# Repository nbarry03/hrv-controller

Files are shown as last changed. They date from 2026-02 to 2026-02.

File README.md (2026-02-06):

# HRV Controller
>**Warning: This is an overview and is not intended to be an exhaustive guide. Use your own judgement and don't burn your house down.**

This project was created to control an HRV system with a [4 wire remote](https://my.daikinnortheast.com/product/control-ventilation-advanced-wall/01tRn000006Wke3IAC). Many smart thermostats can integrate with and control an HRV, but my thermostat only works with 2 wire remote systems, and therefore could not directly be connected.

An ESP8266 with a DAC was used to spoof the remote signals described below, triggering the HRV to run based on the combination of voltages. Because the ESP8266 has wifi and can be integrated into ESPHome, this allows me to use ESPHome to write firmware and control the state of the remote through Home Assistant, or in my case, controlled by AppDaemon and interacting with HASS via the AppDaemon HASS integration.

# The remote
The remote has 4 modes; econo, vent, 20 min/hr, and off. Econo runs the system with a low fan speed, while 20 min/hr runs at max speed but intermittently. Vent runs the system with the fan max speed. The control voltages for each mode are summarized below, with the wire color and remote terminal label denoted as follows: `Wire color (remote label)`.

| Mode | Red (R) | Blue (Bl) | Green (G) | Black (W) |
| --- | --- | --- | --- | --- |
| **Econo** | 5V | - | 3.4V | 3.1V |
| **Vent** | 5V | - | 3.4V | 3.1V |
| **20 min/hr** | 5 | - | 4.4V | 2.0V |
| **Off** | 5V | - | 1.4V | 2.0V |

> ***Note:** The black wire connected to the W terminal.

Based on the measured voltages there are 2 signal wires, green (G) and black (W), with voltage from red (R) and blue (Bl) as ground. Setting the voltages on the green (G) and black (W) signal wires results in the selection of a ventilation mode.

# BOM
| Part | Qty | Note |
| --- | --- | --- |
| ESP8266 | 1 | I used this because it was what I had on hand and worked nicely with the shields below. There may be a more modern alternative like a [Seeed Studio XIAO](https://www.google.com/search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) |
| [Protoboard shield for Wemos D1-Mini](https://www.aliexpress.com/item/1005008599746081.html?spm=a2g0o.order_list.order_list_main.15.1d2518022HH3uu) | 1 | Soldered headers to attach some screw terminals (I believe for 5V and Gnd). This isn't required if you don't mind wires hanging off |
| [PCB screw terminal block](https://www.aliexpress.com/item/1005006363650525.html?spm=a2g0o.order_list.order_list_main.20.1d2518022HH3uu) | 1x 2 pin terminal | For 5V and Gnd screw terminals. The signal wires are not connected in the same way since the signal voltages come from a separate board. |
| STEMMA QT/Qwiic JST SH 4-pin cable (30mm) | 2 | Connects the I2C shield to the I2C level shifter and DAC |
| [TFT 0.85 shield (display)](https://www.aliexpress.com/item/1005006839059889.html?spm=a2g0o.order_list.order_list_main.35.1d2518022HH3uu) | 1 | (Optional) I originally thought a display might be useful, but it has been tricky to set up and I barely look at it. |
| [MCP4728 Quad DAC](https://www.aliexpress.com/item/1005008471916833.html?spm=a2g0o.order_list.order_list_main.50.1d2518022HH3uu) | 1 | Communicates via I2C and sets the signal voltages. |
| [STEMMA QT 3V to 5V level booster](https://www.digikey.ca/en/products/detail/adafruit-industries-llc/5649/21283813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) | 1 | Boosts the 3.3V signal from the ESP8266 to a max of 5V. Required since the controller uses voltages up to 4.4V while the ESP8266 can only output 3.3V |
| M3 heatset insert | 4 | For attaching the DAC and level booster stack to the face plate |
| M1.7 3mm screws | 4 | I think this was the size I ended up using, but am not 100% sure... They need to be pretty small though. These attach the screen and ESP/shield stack to the faceplate. |
| [TFT I2C shield](https://www.aliexpress.com/i/32846977179.html) | 1 | For I2C communication to the level booster and DAC. |

> **Note:** Some ESP8266 models are clones of the Wemos D1 Mini and have the same IO pinout, which is what the shield boards are designed for. Not all ESP8266 dev boards are compatable and may have different pinouts. Be sure to double check that the pins match if you are using these shields.

The required 3D prints are provided in [stl](./stl/). You will need 1 face plate and 4 of the spacers for the DAC and level booster stack.

# Assembly
## ESP8266 stack
The ESP8266 stack was assembed using a combination of header pins for each board in the order below.

```
ESP8266
-------------------------
Protoboard (5V and Gnd screw terminals)
-------------------------
I2C shield
-------------------------
TFT 0.85 shield (display)
-------------------------
Faceplate
```

assembly

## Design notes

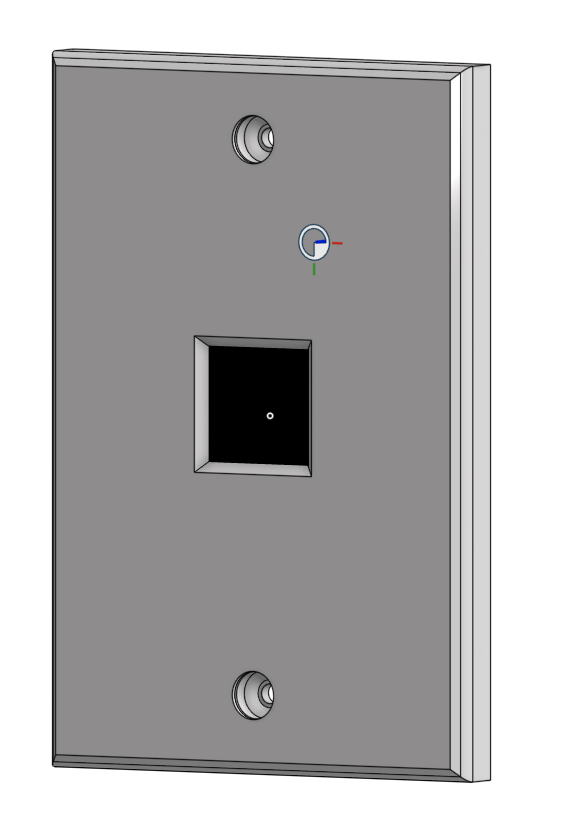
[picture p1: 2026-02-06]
img/faceplate_front_full.png

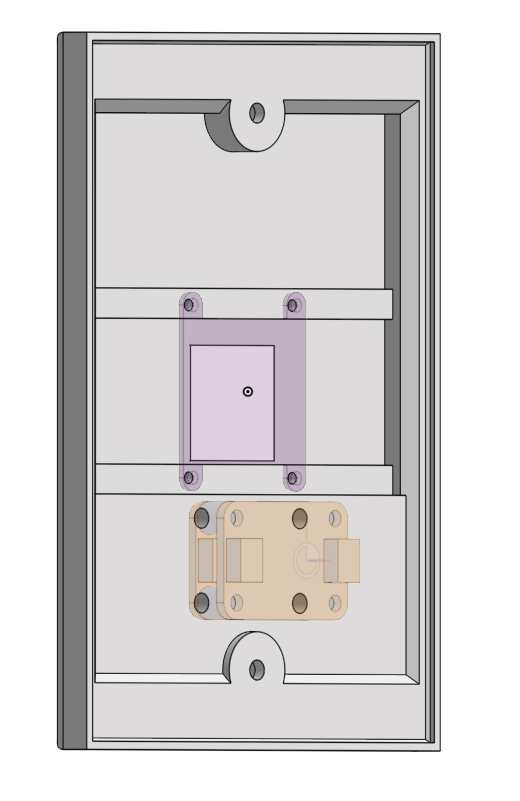
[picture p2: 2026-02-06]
img/faceplate_back.png

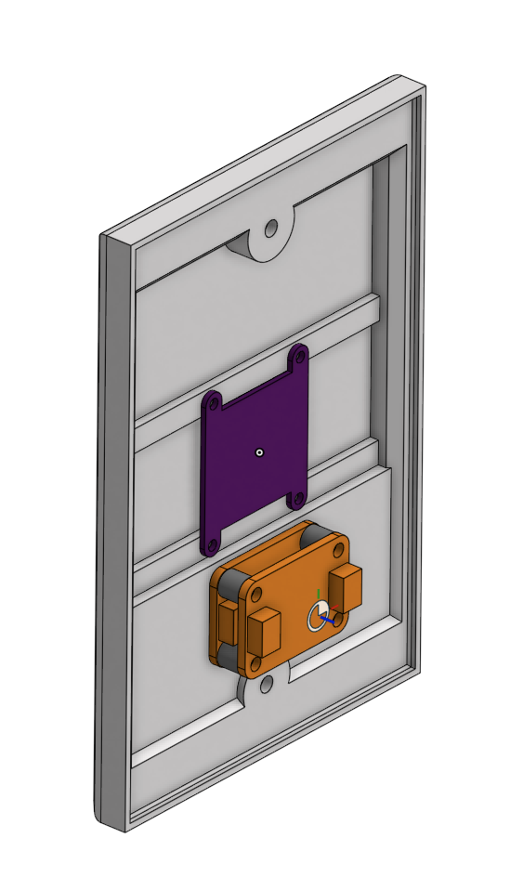
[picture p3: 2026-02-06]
img/faceplate_back_full.png

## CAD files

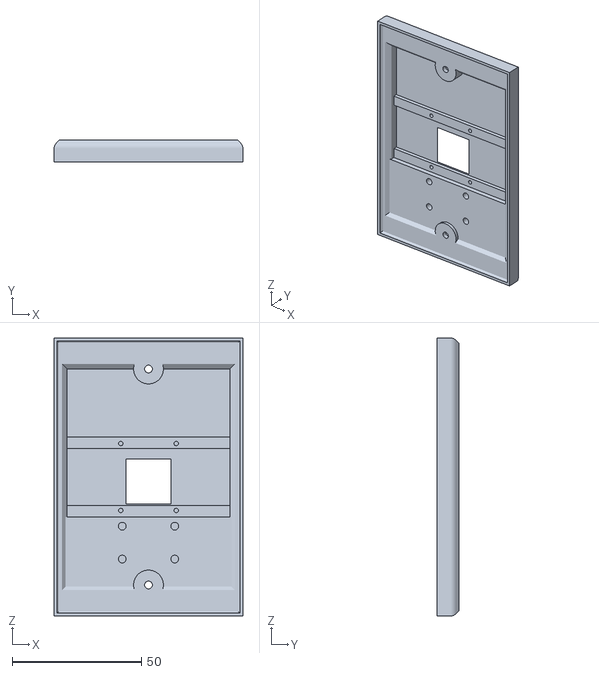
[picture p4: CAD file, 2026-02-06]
stl/HRV controller - Face plate x1.stl
73.0 x 8.40 x 107.5

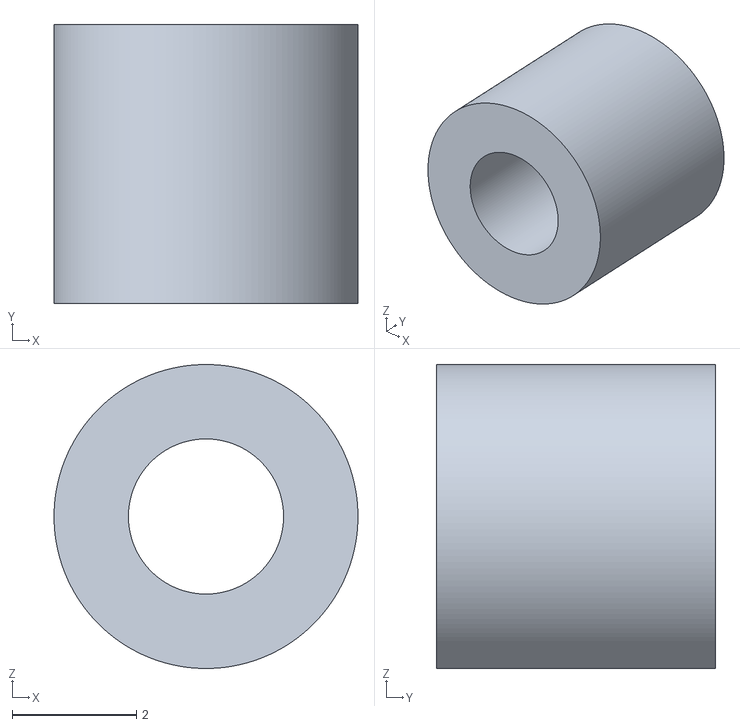
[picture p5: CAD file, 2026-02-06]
stl/HRV controller - Spacer x4.stl
4.90 x 4.50 x 4.90
